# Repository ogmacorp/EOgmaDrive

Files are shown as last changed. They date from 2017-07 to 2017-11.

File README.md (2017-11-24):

<!---
  EOgmaDrive
  Copyright(c) 2017 Ogma Intelligent Systems Corp. All rights reserved.

  This copy of EOgmaDrive is licensed to you under the terms described
  in the EOGMADRIVE_LICENSE.md file included in this distribution.
--->

# EOgmaDrive

Repository for the EOgmaNeo-based self driving car (SDC).

Three sub-directories contain Readme.md files that further describes each configuration. A summary for each configuration is presented below.

Included are two configurations (1 & 2) used to build a 1/10 scale 2WD RC self driving car, and a third configuration to create a hand-sized 3D printed self driving car (uSDC).

**Configuration1** was used in producing the following Ogma YouTube video:

<a href="http://www.youtube.com/watch?feature=player_embedded&v=0ibVhtuQkZA
" target="_blank">Self Driving Car Learns Online and On-board on Raspberry Pi 3</a>

**Configuration3** appears in the first issue of the [HackSpace magazine](https://hackspace.raspberrypi.org/issues/1) (December 2017), as a project on [HackADay.io](https://hackaday.io/project/27173-a-self-driving-car-using-a-raspberry-pi-zero), and was used in producing the following Ogma YouTube video:

<a href="http://www.youtube.com/watch?feature=player_embedded&v=9GNbVkMb8Qw
" target="_blank">World's Smallest Self-Driving Car - a Raspberry Pi Zero on wheels..</a>

As seen in the above video, an [InfiniTrax](http://infinitrax.com/product.php) "1080 BEAST" modular track was used with the uSDC.

A [Unity](https://unity3d.com/) based simulation [OgmaDrive](https://github.com/ogmacorp/OgmaDrive) was used to prototype the SDC, using C# scripts and the EOgmaNeo library.

## Configuration1

- Steam Controller with wireless dongle

SDC:

- Traxxas Rustler RC car
- Raspberry Pi3
- Pi Camera v2
- Pi Camera case
- Active cooling case "Eleduino Raspberry Pi 3 and Raspberry Pi 2 Model B Acrylic Case with High Quality Mini Fan"
- 2 pcs 18650 batteries with battery pack (for powering the steering servo)
- Arduino UNO
- Breadboard
- Anker PowerCore 10000 (for powering the Pi)
- Using fast event-based version of EOgmaNeo + OpenCV's Canny Edge + PySerial (for Arduino communication)

RF Version Extra:

- Pi-Top with Raspberry Pi 3
- Arduino UNO (or Leonardo, USB to RPi)
- RF Transmitter/Receiver Modules "Makerfocus 2pcs Wireless Module NRF24L01+PA+LNA in Antistatic Foam Arduino Compatible with Antenna"

## Configuration2

Base station, for limited communication with the SDC:

- Pi-Top
- Raspberry Pi3
- Arduino UNO (or Leonardo, USB to RPi)
- XBee Arduino shield (v1.0 or modified v1.3)
- XBee Pro (S1, with u.fl antenna)

SDC:

- Traxxas Rustler RC car (optional clear body)
- Raspberry Pi3
- Raspberry Camera (mounted to front bumper)
- Pimoroni Pibow case
- Freetronics PiLeven (i2c to RPi, UART to XBee)
- XBee Arduino shield (v1.0 or modified v1.3)
- XBee Pro (S1, u.fl antenna)
- Power Bank (to PiLeven or RPi)
- Servo pass-through connector (attached to PiLeven)

## Configuration3

- Steam Controller with wireless dongle
- InfiniTrax modular track system (optional)

uSDC:

- 3D Printed base, RPi ZeroW mount, and camera mount
- Raspberry Pi ZeroW
- Pimoroni Explorer pHAT (motor drivers)
- Pololu 136:1 sub-micro planetary gearmotors, wheels, and front ball caster
- Adafruit Lithium Ion Polymer Battery, with a PowerBoost and charger module
- SainSmart wide angle camera

## License and Copyright

<br />The work in this repository is licensed under the <a rel="license" href="http://creativecommons.org/licenses/by-nc-sa/4.0/">Creative Commons Attribution-NonCommercial-ShareAlike 4.0 International License</a>. See the  [EOGMADRIVE_LICENSE.md](https://github.com/ogmacorp/EOgmaDrive/blob/master/EOGMADRIVE_LICENSE.md) and [LICENSE.md](https://github.com/ogmacorp/EOgmaDrive/blob/master/LICENSE.md) files for further information.

Contact Ogma via licenses@ogmacorp.com to discuss commercial use and licensing options.

EOgmaDrive Copyright (c) 2017 [Ogma Intelligent Systems Corp](https://ogmacorp.com). All rights reserved.

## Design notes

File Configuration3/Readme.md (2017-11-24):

<!---
  EOgmaDrive
  Copyright(c) 2017 Ogma Intelligent Systems Corp. All rights reserved.

  This copy of EOgmaDrive is licensed to you under the terms described
  in the EOGMADRIVE_LICENSE.md file included in this distribution.
--->

# Configuration3 (uSDC)



As seen in the first issue of the [HackSpace magazine](https://hackspace.raspberrypi.org/issues/1) (December 2017), and as a project on [HackADay.io](https://hackaday.io/project/27173-a-self-driving-car-using-a-raspberry-pi-zero)

## Bill of Materials

The [BillOfMaterials.md](BillOfMaterials.md) file details all the items required before assembly.

## Hardware Assembly

Refer to the [AssemblyInstructions.md](AssemblyInstructions.md) file for a detailed description of the assembly steps.

## Software Installation

The [SoftwareInstallation.md](SoftwareInstallation.md) file contains all the steps required to install and test package dependencies.

## Control of the uSDC

There are two Python3 scripts included in this repository to test the uSDC:

- motorTest.py - A script to test the Explorer pHAT, Steam controller, and drive the uSDC around.
- main.py - The main script containing using the EOgmaNeo library. Allowing for learning, inference, and self-driving on the RPi ZeroW.

### Steam controller daemon

Both of the included python scripts require the Steam controller daemon to be running. After the daemon has been started, it emulates the Steam controller as a Xbox controller. PyGame can then connect to and obtain joystick and button information. The motorTest.py and main.py scripts can then make use of the controller to drive the uSDC around.

Starting the daemon requires the following bash command:

```bash
sudo python3 ~/steamcontroller/scripts/sc-xbox.py start
```

and the following command to stop the daemon:

```bash
sudo python3 ~/steamcontroller/scripts/sc-xbox.py stop
```

### motorTest python script

To test the Steam controller and Explorer pHAT motor driver, the following commands and script can be used:

```bash
cd ~/EOgmaDrive/Configuration3
sudo python3 ~/steamcontroller/scripts/sc-xbox.py start
sudo python3 motorTest.py
sudo python3 ~/steamcontroller/scripts/sc-xbox.py stop
```

Similar controls as used in the main.py script are used here:

- The joystick controls left or right steering,
- Trigger buttons apply forward/backward drive,
- The `A` button cleanly exits the script.

The `trimming` global variable allows for trimming of the forward/backward motion, so that applying motion using the triggers ensures that the uSDC travels in a straight line.

## The main python script

The `main.py` Python3 script is used for training (manual driving) and inference (self driving). All processing occurs on the Raspberry Pi ZeroW board.

It can be started using the following bash commands:

```bash
cd ~/EOgmaDrive/Configuration3
sudo python3 ~/steamcontroller/scripts/sc-xbox.py start
sudo python3 main.py
sudo python3 ~/steamcontroller/scripts/sc-xbox.py stop
```

The uSDC can then be controlled using the Steam controller with:

- The analogue joystick controls left or right steering.
- Trigger buttons apply forward/backward drive.
- The `A` button toggles between training and prediction modes.
- The `B` button saves the current camera image.
- The `X` button saves the current state of the hierarchy.
- The `Y` button exits the script.

If you train and save out the current state of the hierarchy, that saved state can be reloaded by starting the script with a `load` parameter. For example:

```bash
sudo python3 main.py load
```

**Note:** Saving the hierarchy to the a file on the SD card can take a minute or so to perform. Console text will announce when saving starts, and also when saving has completed.

If the uSDC doesn't travel in a straight line using one of the trigger buttons, a `trimming` global variable can be modified to compensate for any drift. For example this could be set to `trimming = 0.2`

An `RGB` image is captured from the camera module at each time step. This is converted into a grey scale image. And an EOgmaNeo pre-encoder (`ImageEncoder`) is used to transform the dense camera image into a sparse chunked representation, that alongside the current motor values, is sent into the EOgmaNeo predictive hierarchy.

When the `A` button is initially pressed the `training` global variable is toggled. And instead of using the Steam controller input to steer the uSDC and send values into the EOgmaNeo predictive hierarchy (training mode), the hierarchy's prediction of the next motor steering values are used (inference mode). Be aware that during inference mode a constant forward drive is applied to both motors. Pressing the `A` button again can toggle back to training mode.

## Testing the uSDC

Online learning only occurs within the `main.py` script and the EOgmaNeo predictive hierarchy when forward drive is active. To navigate around a track, a number of laps are required before the predictive hierarchy can confidently make steering predictions.

With learning only enabled during forward motion, it's possible to reverse out of steering mistakes made when driving around a track.

The more laps of a track that occur during training mode, the more confident the predictive hierarchy will be when switching to inference mode (that is, steering only use hierarchy output predictions and current camera input).

As seen in our YouTube video of the uSDC, we use an [InfiniTrax](http://infinitrax.com/product.php) modular track to perform more elaborate training and inference testing.

<a href="http://www.youtube.com/watch?feature=player_embedded&v=9GNbVkMb8Qw
" target="_blank">World's Smallest Self-Driving Car - a Raspberry Pi Zero on wheels..</a>

The simplest way to check that everything is working is to perform the following:

1. Apply constant left/right steering.
1. Apply forward drive so that the uSDC spins on the spot.
1. After 30-60 seconds, release the joystick and trigger button.
1. Press the `A` button, and the uSDC should spin on the spot.
1. Press the `A` button again to toggle back to training mode.

Try the above but steering in the opposite direction. And test out saving and reloading of the hierarchy to see whether it remembers how to spin on the spot.

## License and Copyright

<br />The work in this repository is licensed under the <a rel="license" href="http://creativecommons.org/licenses/by-nc-sa/4.0/">Creative Commons Attribution-NonCommercial-ShareAlike 4.0 International License</a>. See the  [EOGMADRIVE_LICENSE.md](https://github.com/ogmacorp/EOgmaDrive/blob/master/EOGMADRIVE_LICENSE.md) and [LICENSE.md](https://github.com/ogmacorp/EOgmaDrive/blob/master/LICENSE.md) file for further information.

Contact Ogma via licenses@ogmacorp.com to discuss commercial use and licensing options.

EOgmaDrive Copyright (c) 2017 [Ogma Intelligent Systems Corp](https://ogmacorp.com). All rights reserved.

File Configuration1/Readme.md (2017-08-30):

<!---
  EOgmaDrive
  Copyright(c) 2017 Ogma Intelligent Systems Corp. All rights reserved.

  This copy of EOgmaDrive is licensed to you under the terms described
  in the EOGMADRIVE_LICENSE.md file included in this distribution.
--->

# Configuration1

Parts:

- Traxxas Rustler 
- Raspberry Pi 3
- Anker Powercore 10000
- Arduino Uno R3
- Steam Controller (w/ dongle)
- Elduino Pi 3 case with mini fan
- Pi Camera v2
- Pi Camera Case (blue)
- 2x EBL 18650 3.7v 3000mAh Li-ion Rechargable Batteries (for Arduino)
- 18650 2 battery holder
- Miscellaneous: Wires, breadboard, charger (for 18650), double-sided foam tape, crimps

## Overview of Configuration

The Steam controller is used to remotely control the car for training. The Pi communicates with the Arduino using serial, where the Pi sends the Arduino motor commands for the steering/throttle. The Anker PowerCore powers the Pi 3, and high-drain 18650 Li-ion batteries are used to power the Arduino/servo/ESC (not enough amps from just the PowerCore).

An older version of this configuration had the Steam controller communicate with a Pi-Top instead of the car directly, and then used a radio module to communicate with the car. However, just using the steam controller directly improved responsiveness and range is sufficient. The Steam controller dongle is now plugged directly into the Pi 3, where it uses an Xbox360 emulation driver to allow Pygame to detect it [https://github.com/ynsta/steamcontroller](https://github.com/ynsta/steamcontroller).

- SDC\_Transmitter.ino contains the old transmitter code for the older RF version of this configuration (no longer used)
- SDC\_controller.ino contains the old receiver code for the older RF version of this configuration (no longer used)
- SDC\_controller\_norf.ino contains the final (no RF) code used in the Arduino
- SDC3\_sc.py, sdc\_fast\_line.py, and sdc\_master\_sc.py contain the Pi 3 controller scripts. These are all variations of each other, but the sdc\_fast\_line version performs the best.

Images:

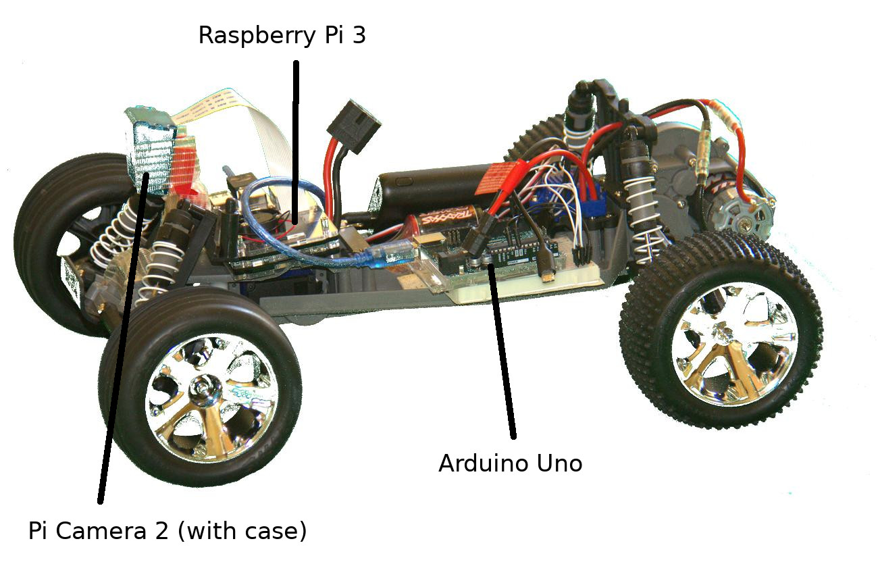
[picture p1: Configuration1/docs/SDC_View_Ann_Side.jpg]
View1


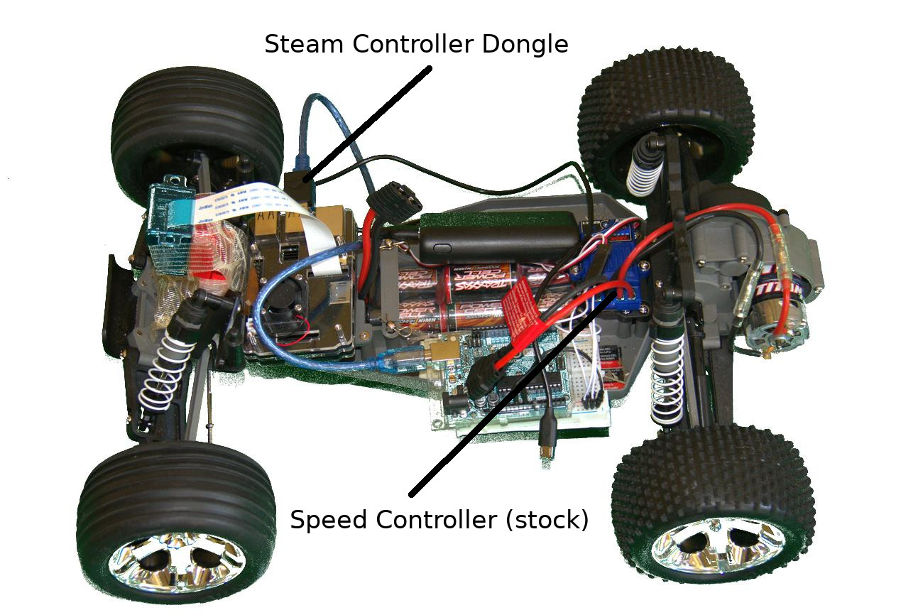
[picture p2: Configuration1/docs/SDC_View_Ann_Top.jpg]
View2


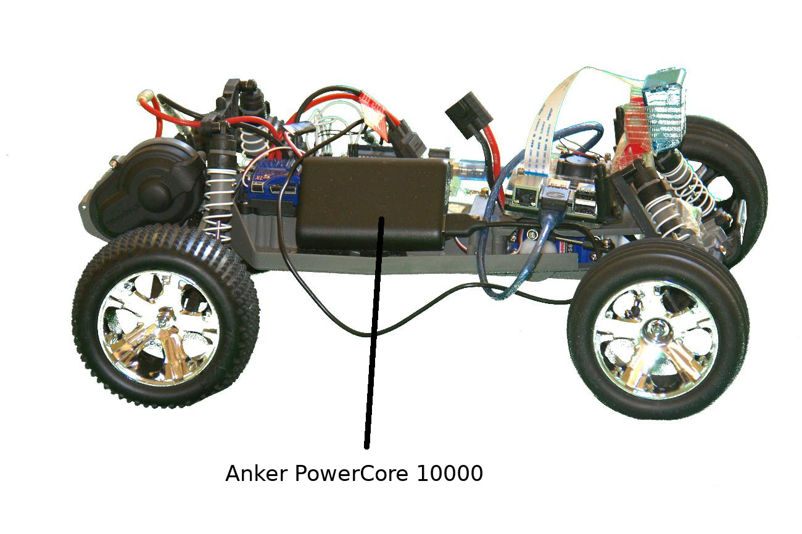
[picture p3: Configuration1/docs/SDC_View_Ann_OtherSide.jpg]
View3


## License and Copyright

<br />The work in this repository is licensed under the <a rel="license" href="http://creativecommons.org/licenses/by-nc-sa/4.0/">Creative Commons Attribution-NonCommercial-ShareAlike 4.0 International License</a>. See the  [EOGMADRIVE_LICENSE.md](https://github.com/ogmacorp/EOgmaDrive/blob/master/EOGMADRIVE_LICENSE.md) and [LICENSE.md](https://github.com/ogmacorp/EOgmaDrive/blob/master/LICENSE.md) file for further information.

Contact Ogma via licenses@ogmacorp.com to discuss commercial use and licensing options.

EOgmaDrive Copyright (c) 2017 [Ogma Intelligent Systems Corp](https://ogmacorp.com). All rights reserved.

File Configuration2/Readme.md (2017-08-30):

<!---
  EOgmaDrive
  Copyright(c) 2017 Ogma Intelligent Systems Corp. All rights reserved.

  This copy of EOgmaDrive is licensed to you under the terms described
  in the EOGMADRIVE_LICENSE.md file included in this distribution.
--->

# Configuration2

# Base station

The PiTop base station is only required to toggle between training and prediction modes on the SDC. And to optionally allow for a SSH shell, and/or remote desktop, into the SDC RPi for diagnostic purposes.

- [Pi-Top](https://pi-top.com)
- [Raspberry Pi3](https://www.raspberrypi.org)
- [Arduino](https://www.arduino.cc) UNO (or Leonardo, connected via USB to RPi)
- [XBee Arduino shield](https://www.arduino.cc/en/Main/ArduinoXbeeShield) (v1.0 or modified v1.3)
- [XBee Pro](https://www.digi.com/lp/xbee) (Series 1, with u.fl antenna)
- [USB WIFI (802.11 b/g/n) adapter](https://thepihut.com/products/usb-wifi-adapter-for-the-raspberry-pi) (Optional)

Image 1: PiTop with an Arduino Uno and XBee Pro RF module and antenna.  
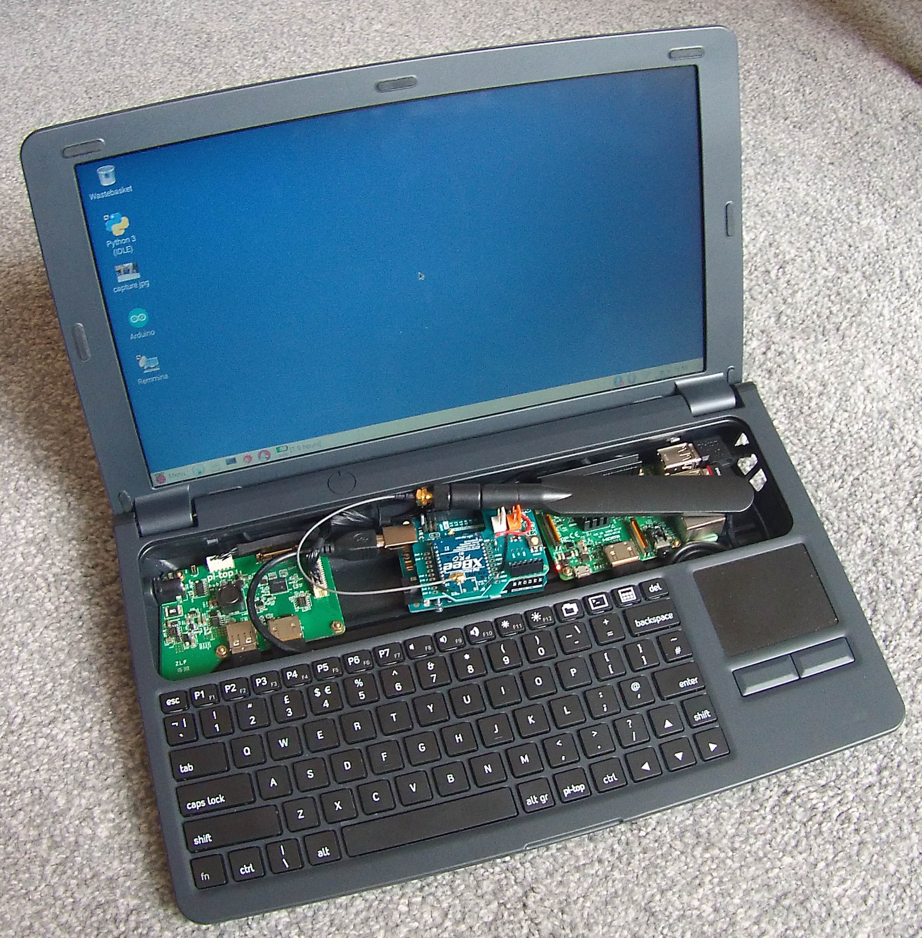
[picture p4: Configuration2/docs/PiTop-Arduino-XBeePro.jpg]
PiTop


## Optional: Pi-Top as a WiFi Access Point and DHCP server

The Raspibery Pi3 installed into the Pi-Top can be setup as a WiFi access point and DHCP server. This allows for the RPi on the SDC to wirelessly connect to the Pi-Top RPi, and for a SSH shell to be created on the Pi-Top RPi.

Instructions for how to set this up can be found here: https://learn.adafruit.com/setting-up-a-raspberry-pi-as-a-wifi-access-point/overview

Connection range is limited when using WiFi, so this is only required to be able to access the SDC RPi when on the field/track.

## Arduino XBee Shields

Using an Arduino board that uses a single UART for both USB and shield communication (D0 and D1), such as the Uno or Duemilanove, requires modification to the shield dependant on the version:

- v1.0 ./docs/XbeeShieldSchematic.pdf  
For the v1.0 version of the shield it is simply a case of removing the jumpers on JP2 and JP3. Then connecting pin 2 of JP2 to pin 3 of J1 (D2 on the Arduino), and pin 2 of JP3 to pin 4 of J1 (D3 on the Arduino).

- v1.3 ./docs/Arduino_Shield_Xbee_Rev1_3.pdf  
For the v1.3 version of the shield two tracks need to be cut (tracks B and E out of SW1). Then connecting pin 2 of XB1 to pin 3 of J1 (D2 on the Arduino), and pin 2 of IC2 to pin 4 of J1 (D3 on the Arduino).

This modification then allows the Arduino SoftwareSerial library to use D2 (Rx) and D3 (Tx) to communicate exclusively with the XBee Pro.

*NOTE 1:* When using the XBee shield with the PiLeven this modification is not required. The PiLeven and RPi can communicate via an i2c interface.  
*NOTE 2:* An alternative method would be to use an Arduino Leonardo. That creates a CDC-ACM USB connection with the RPi, leaving the Leonardo UART to be used with the XBee Pro.

## PiTop to SDC communication

PiTop RPi Python serial connection to the Arduino (over USB). Arduino connection to the XBee Pro RF module. Upload the `Configuration2/PiTop_XBee_CommTest` sketch to the Arduino. Use the Arduino IDE Serial Monitor to send the following key commands to the SDC Arduino:

- `T` to enter training mode,
- `P` to enter prediction mode,
- `S` to receive the Actual and Predicted steering and throttle values.
- `V` to receive information on the steering and throttle PWM signals.

# SDC

Image 2: The Traxxas Rustler showing the front bumper mounted Raspberry Pi3 camera, blue RF antenna that connects to the Traxxas stock controller, and the black top mounted XBee Pro antenna that connects to the PiTop-housed XBee Pro module.  
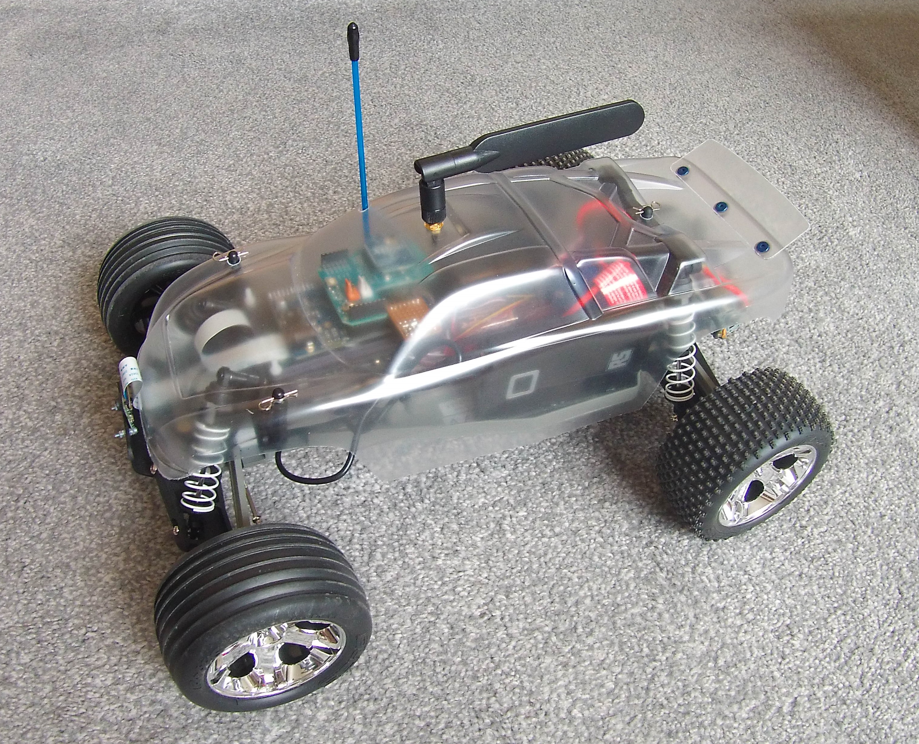
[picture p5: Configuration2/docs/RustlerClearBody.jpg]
Traxxas Rustler
 

- [Traxxas Rustler](https://traxxas.com/products/models/electric/37054rustler) RC car (optional clear body)
- [Raspberry Pi3](https://www.raspberrypi.org) (v2, FOV 62.2x48.8 degrees)
- [Raspberry Pi Camera](https://www.raspberrypi.org/products/camera-module-v2/) (mounted to front bumper)
- [Pimoroni Pibow case](https://shop.pimoroni.com/collections/pibow)
- [Freetronics PiLeven](https://www.freetronics.com.au/collections/raspberry-pi/products/pileven-arduino-compatible-expansion-for-raspberry-pi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) (Arduino compatble, i2c to RPi, UART to XBee)
- [XBee Arduino shield](https://www.arduino.cc/en/Main/ArduinoXbeeShield)
- [XBee Pro](https://www.digi.com/lp/xbee) (Series 1, with u.fl antenna)
- [Power Bank](http://uk.rs-online.com/web/p/power-banks/7757508/) (at least 2A @ 5V, to PiLeven or RPi)
- Servo pass-through connector (attached to PiLeven)

Image 3: Internal components - RPi3 in a grey Pimoroni Pibow case, connected to a PiLeven RPi hat, connected to a XBee Pro RF module and shield, a protoboard servo pass-through connecter intercepting the front servo and ESC connections, a front bumper mounted RPi camera v2, and a 2A Power bank for powering the RPi3 and PiLeven.  
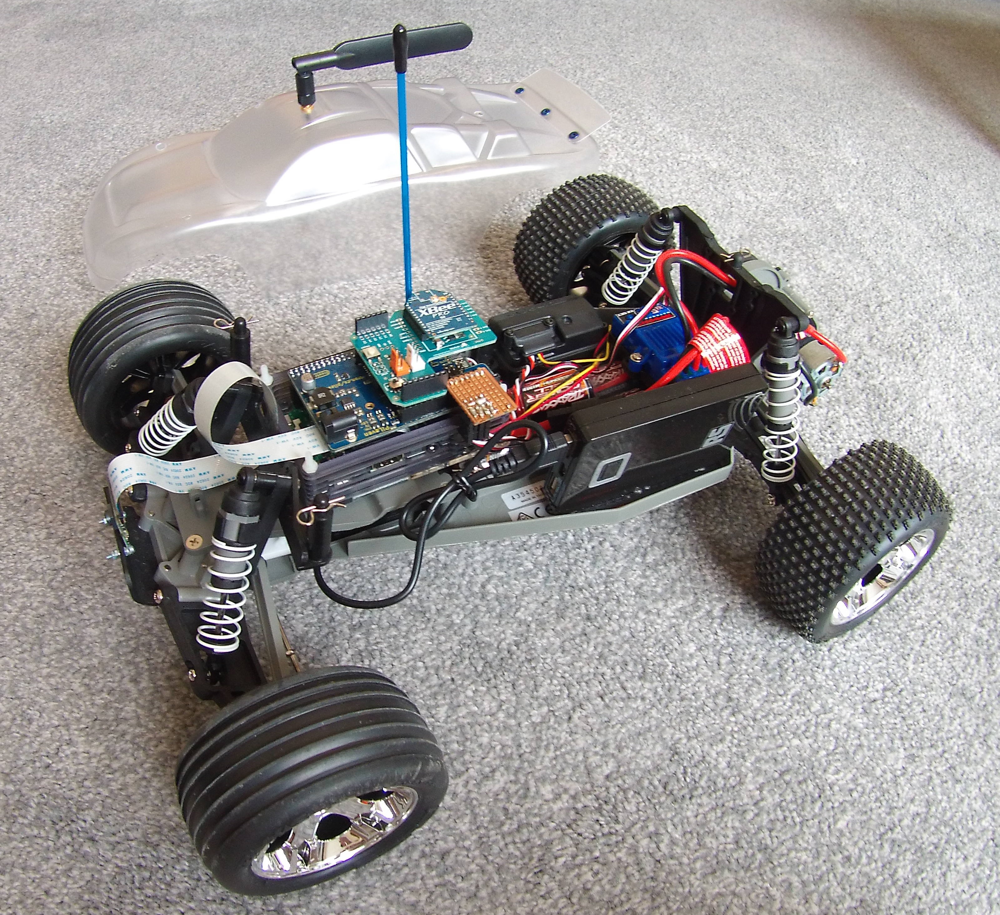
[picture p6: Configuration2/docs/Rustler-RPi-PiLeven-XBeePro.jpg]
Internal setup


## PiLeven (Arduino) RPi hat

Using a PiLeven RPi hat allows for the use of i2c communications with the SDC RPi. Freeing up the PiLeven UART for use by the XBee Pro RF unit.

### PiLeven_XBee_CommTest

Python SMBus library for Wire (i2c) communication between RPi and PiLeven. PiLeven (Arduino) Serial UART to XBee Pro communication.

https://github.com/freetronics/PiLeven/wiki/I2C

## Servo pass-through connector

The front steering servo connection with the Traxxas Rustler RF module is intercepted via headers soldered to the PiLeven. With Gnd and Power pass-through, and the signal line connected via D8 and D9 shield connections with the PiLeven (Arduino).

This allows for the PiLeven to monitor the steering PWM signal coming from the Traxxas RF module. This monitored PWM signal is sent to the SDC RPi for input into the EOgmaNeo library, and the predicted steering angle out of EOgmaNeo can then be passed back from the RPi to the PiLeven, to be used as the alternative steering PWM signal. During training the monitored PWM signal can be passed directly though to the front steering servo.

## Throttle pass-through connector

The ESC XL5 motor controller connection with the Traxxas Rustler RF module is intercepted via headers soldered to the PiLeven. With Gnd and Power pass-through, and the signal line connected via D10 and D11 shield connections with the PiLeven (Arduino).

## SDC RPi Controller script

The `RPi_Controller.py` Python script is the main software controlling:
- the EOgmaNeo learning algorithm, 
- communication with the PiLeven and XBee Pro RF module,
- handling the RPi camera image stream (Yuv format, only Y/Luminance used),
- using Pillow to perform edge-filtering of the Luminance camera image,
- receiving steering angles from the PiLeven,
- predicting steering angles and forwarding to the PiLeven.

The `PiLeven_Controller` Arduino sketch requires uploading to the PiLeven via the Arduino IDE. It handles:
- communication with the SDC RPi and XBee Pro RF module,
- sends steering value to the SDC RPi,
- receives predicted steering value from the SDC RPi,
- receives via the XBee Pro commands from the Pi-Top.

# Misc

## Python packages

Install OpenCV via https://github.com/jabelone/OpenCV-for-Pi
> pip3 install -r requirements.txt

## Traxxas Rustler vs Unity Stockcar dimensions

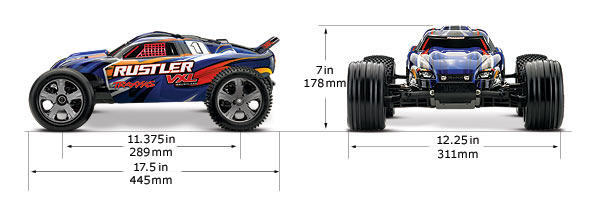
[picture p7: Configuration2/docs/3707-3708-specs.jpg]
Rustler dimensions
  
http://rustlervxlguide.blogspot.co.uk/2012/03/rustler-vxl-specs-from-traxxas.html

| | Traxxas Rustler | Unity Stockcar model |
|---|---|---|
| Length | 44.5 cm | 2 units |
| Width  | 31.1 cm | 0.75 units |
| Height | 17.8 cm | 0.6 units |

## License and Copyright

<br />The work in this repository is licensed under the <a rel="license" href="http://creativecommons.org/licenses/by-nc-sa/4.0/">Creative Commons Attribution-NonCommercial-ShareAlike 4.0 International License</a>. See the  [EOGMADRIVE_LICENSE.md](https://github.com/ogmacorp/EOgmaDrive/blob/master/EOGMADRIVE_LICENSE.md) and [LICENSE.md](https://github.com/ogmacorp/EOgmaDrive/blob/master/LICENSE.md) file for further information.

Contact Ogma via licenses@ogmacorp.com to discuss commercial use and licensing options.

EOgmaDrive Copyright (c) 2017 [Ogma Intelligent Systems Corp](https://ogmacorp.com). All rights reserved.

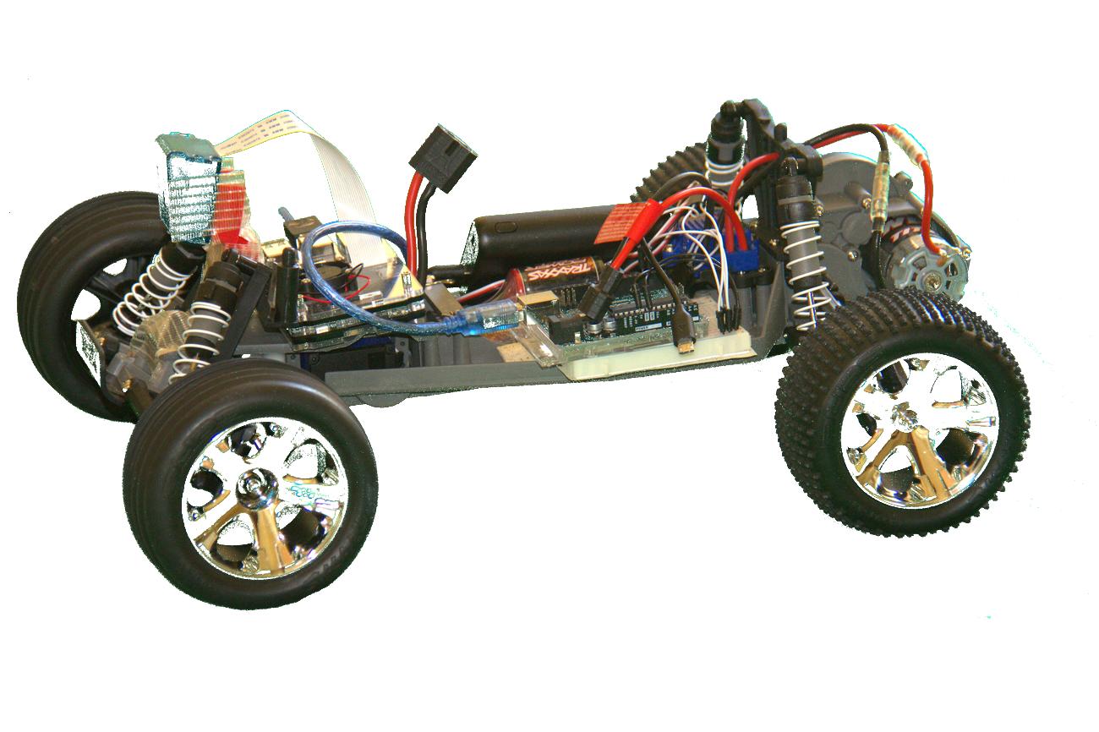
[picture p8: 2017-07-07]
Configuration1/docs/SDC_View_Side.jpg

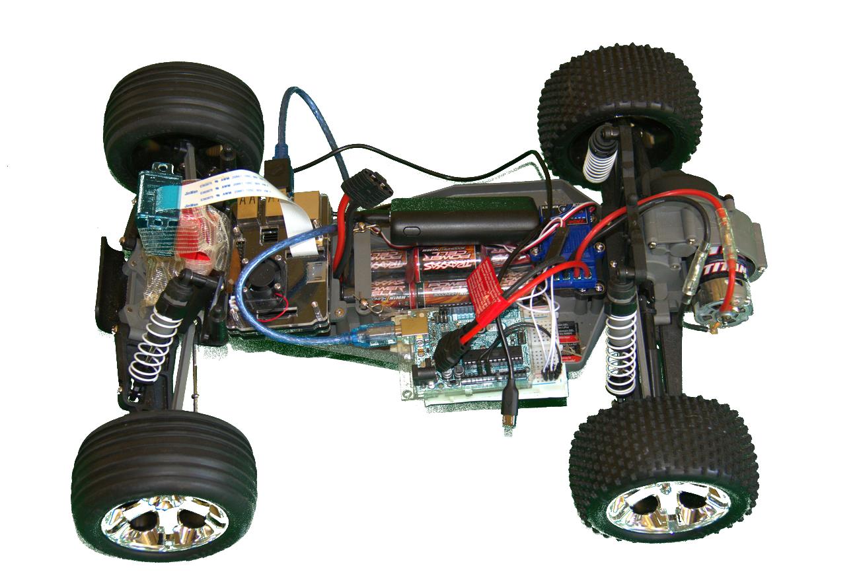
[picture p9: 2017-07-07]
Configuration1/docs/SDC_View_Top.jpg

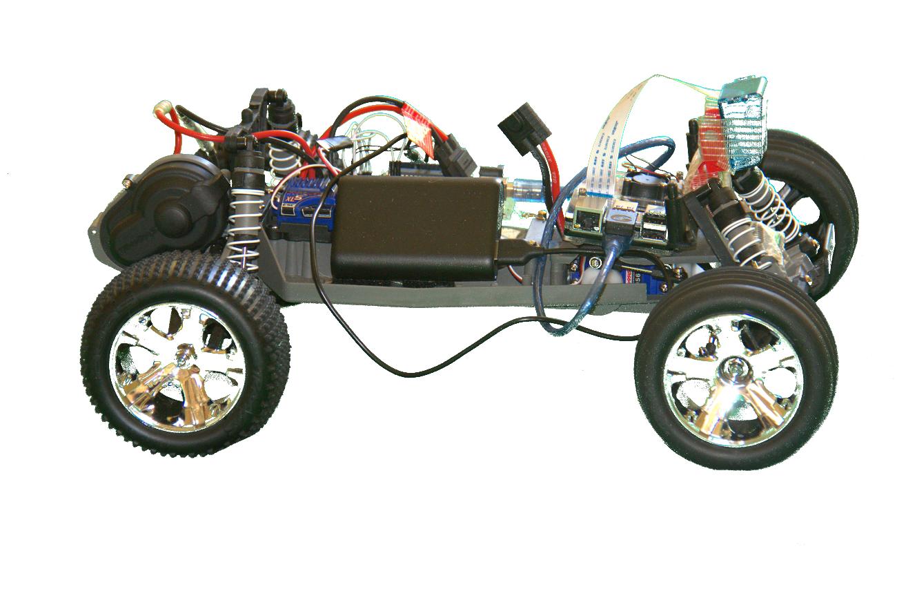
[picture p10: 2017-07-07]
Configuration1/docs/SDC_View_OtherSide.jpg

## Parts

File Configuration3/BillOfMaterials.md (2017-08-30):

<!---
  EOgmaDrive
  Copyright(c) 2017 Ogma Intelligent Systems Corp. All rights reserved.

  This copy of EOgmaDrive is licensed to you under the terms described
  in the EOGMADRIVE_LICENSE.md file included in this distribution.
--->

# Configuration3 (uSDC)



## Bill of Materials

Refer to the following tables for details of the numbered items in this image:
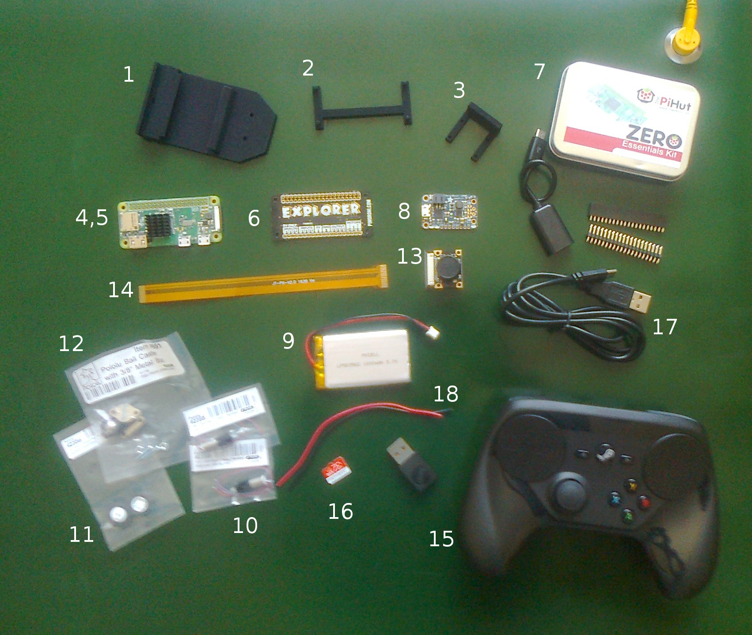
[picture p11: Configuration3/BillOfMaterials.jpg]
Bill Of Materials


### 3D printed parts

| Item # | STL Filename | Description |
| --- | --- | --- |
| 1 | base.stl | Main base for the uSDC |
| 2 | piMount.stl | Mounting frame for Pi ZeroW |
| 3 | camMount.stl | Mount for RPi camera |

Notes:

1. The main base part has three through holes: One rear diagonal hole that allows the motor cables to thread through from the mounting cylinder for the motors. And two front holes (13.462mm spacing) for mounting the ball caster.
1. The Pi ZeroW and Camera mounting parts require the appropriate glue to position them onto the base platform. The type/kind of glue is dependant on the material used when 3D printing all the parts. For example, when a Nylon PA2200 based material is used Araldite (epoxy adhesive) is recommended.

### Electro-mechanical parts

| Item # | Manufacturer | Description | Part # |
| --- | --- | --- | ---: |
| 4 | [Raspberry Pi](https://www.raspberrypi.org/) | Main processing board | [Zero W](https://www.raspberrypi.org/products/raspberry-pi-zero-w/) |
| 5 | - | Heatsink for the Raspberry Pi Zero Broadcom CPU (~6mm height) | [example](https://shop.pimoroni.com/products/heatsink) |
| 6 | [Pimoroni](https://shop.pimoroni.com/) | Pi Zero HAT containing two H-bridge motor drivers | [Explorer pHAT](https://shop.pimoroni.com/products/explorer-phat) |
| 7 | [The Pi Hut](https://thepihut.com/) | Pi Zero Essentials Kit that *importantly* includes a male MicroUSB to female USB adapter, and dual-row male and female GPIO headers | [Zero Essentials Kit](https://thepihut.com/products/raspberry-pi-zero-essential-kit) |
| 8 | [Adafruit](https://www.adafruit.com/) | PowerBoost 1000 Charger - Rechargeable 5V Lipo USB Boost @ 1A - 1000C | [2465](https://www.adafruit.com/product/2465) |
| 9 | [Adafruit](https://www.adafruit.com/) | Lithium Ion Polymer Battery - 3.7v 1200mAh | [258](https://www.adafruit.com/product/258) |
| 10 | [Pololu](https://www.pololu.com/) | (x2) 136:1 Sub-Micro Plastic Planetary Gearmotor 6Dx19L mm | [2358](https://www.pololu.com/product/2358) |
| 11 | [Pololu](https://www.pololu.com/) | 14×4.5mm Wheel Pair for Sub-Micro Plastic Planetary Gearmotors | [2356](https://www.pololu.com/product/2356) |
| 12 | [Pololu](https://www.pololu.com/) | Ball Caster with 3/8″ Metal Ball | [951](https://www.pololu.com/product/951) |
| 13 | [Sain Smart](https://www.sainsmart.com/) | Wide Angle FOV160° 5MP Camera Module | [101-40-113](https://www.sainsmart.com/sainsmart-wide-angle-fish-eye-camera-lenses-for-raspberry-pi-arduino.html) |
| 14 | [Sain Smart](https://www.sainsmart.com/) | Camera Cable for Raspberry Pi Zero | [101-40-199](https://www.sainsmart.com/raspberry-pi/camera-module/sainsmart-expansion-development-board-support-arduino-xbee-for-raspberry-pi-a-pi-b-pi-2-model-b-pi-3-model-b.htm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) |
| 15 | [Valve](http://www.valvesoftware.com/) | Steam Controller (includes a USB dongle) | [info](http://store.steampowered.com/app/353370/Steam_Controller/) |
| 16 | - | Raspberry Pi Zero compatible micro SD / SDHC card | [examples](http://www.raspberry-pi.co.uk/2012/06/07/compatible-sd-cards/) |
| 17 | - | USB to microUSB data cable (connecting a PC/Laptop to the Pi Zero) | |
| 18 | - | Power hook-up wires (connecting the PowerBoost to Explorer pHAT) | |
| - | - | Tools, e.g. solder and iron, wire cutter, glue, non-conductive Velcro/foam tape, etc. | |
| - | - | Nuts and bolts (for connecting the camera module to the mounting part), e.g. M2 x 10/12mm

Notes:

1. Although the motor shafts have a flattened key on them, the motor wheels do not. Therefore it's typical to use a small amount of glue to attach the wheels to the motor shaft. Be careful not to push/bleed glue into the motor gearbox casing.

### Modular track system (optional)

We used an [InfiniTrax](http://infinitrax.com/product.php) (http://infinitrax.com/product.php) "1080 BEAST" modular track system for testing the uSDC. This track can be seen in the YouTube video of the uSDC - https://www.youtube.com/watch?v=9GNbVkMb8Qw

## License and Copyright

<br />The work in this repository is licensed under the <a rel="license" href="http://creativecommons.org/licenses/by-nc-sa/4.0/">Creative Commons Attribution-NonCommercial-ShareAlike 4.0 International License</a>. See the  [EOGMADRIVE_LICENSE.md](https://github.com/ogmacorp/EOgmaDrive/blob/master/EOGMADRIVE_LICENSE.md) and [LICENSE.md](https://github.com/ogmacorp/EOgmaDrive/blob/master/LICENSE.md) file for further information.

Contact Ogma via licenses@ogmacorp.com to discuss commercial use and licensing options.

EOgmaDrive Copyright (c) 2017 [Ogma Intelligent Systems Corp](https://ogmacorp.com). All rights reserved.

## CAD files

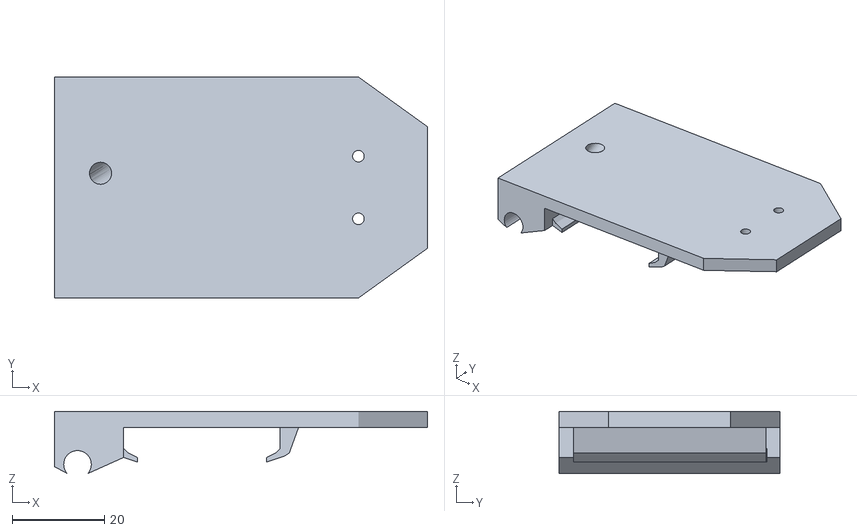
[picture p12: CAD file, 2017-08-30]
Configuration3/base.stl
81.0 x 48.0 x 13.5

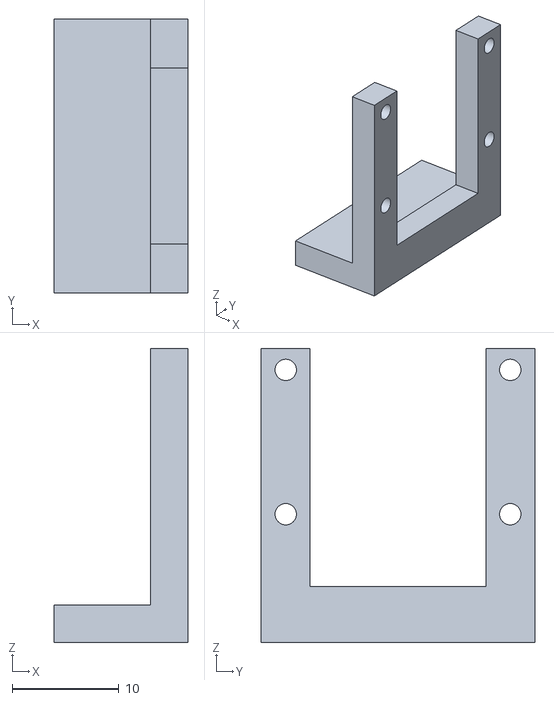
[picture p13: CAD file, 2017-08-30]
Configuration3/camMount.stl
12.5 x 25.6 x 27.5

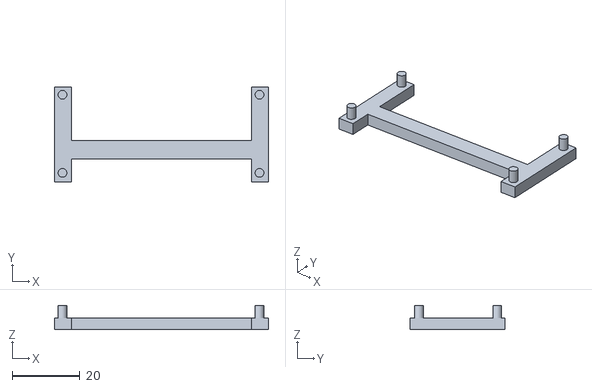
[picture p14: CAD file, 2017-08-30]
Configuration3/piMount.stl
63.0 x 28.0 x 7.21

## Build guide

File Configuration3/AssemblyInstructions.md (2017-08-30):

<!---
  EOgmaDrive
  Copyright(c) 2017 Ogma Intelligent Systems Corp. All rights reserved.

  This copy of EOgmaDrive is licensed to you under the terms described
  in the EOGMADRIVE_LICENSE.md file included in this distribution.
--->

# Configuration3 (uSDC)



## Bill of Materials

Refer to the [BillOfMaterials.md](BillOfMaterials.md) for all the items required before assembly.

## Hardware assembly

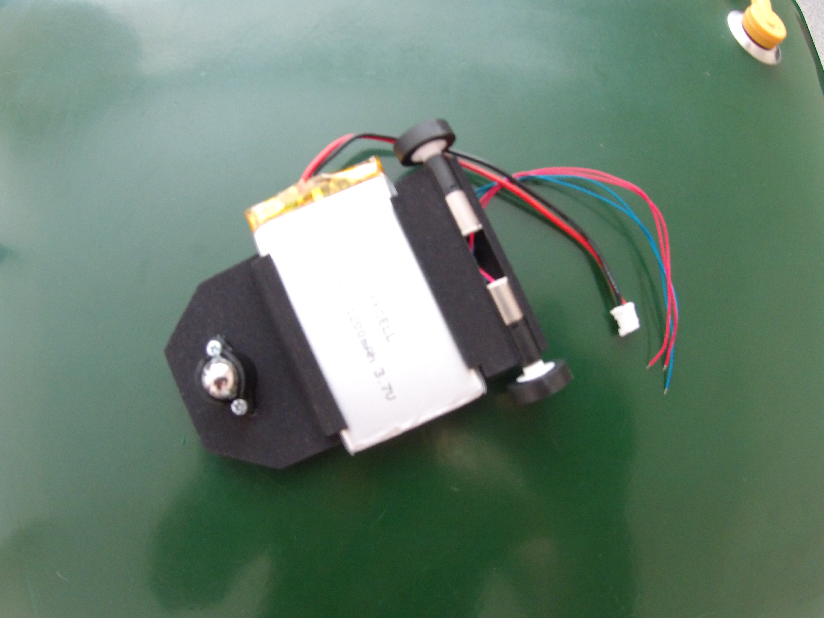
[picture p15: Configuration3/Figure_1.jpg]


Figure 1,

- Glue the wheels to the Pololu motors. Take care not to get any glue into the black motor gearbox casing.
- Slot the motors into the base. Feed the motor cables through the hole in the base.
- Bolt the Pololu ball caster to the base. Use the larger spacing plate supplied with the ball caster.
- Slide the Adafruit LiPo battery into the base.

<br>

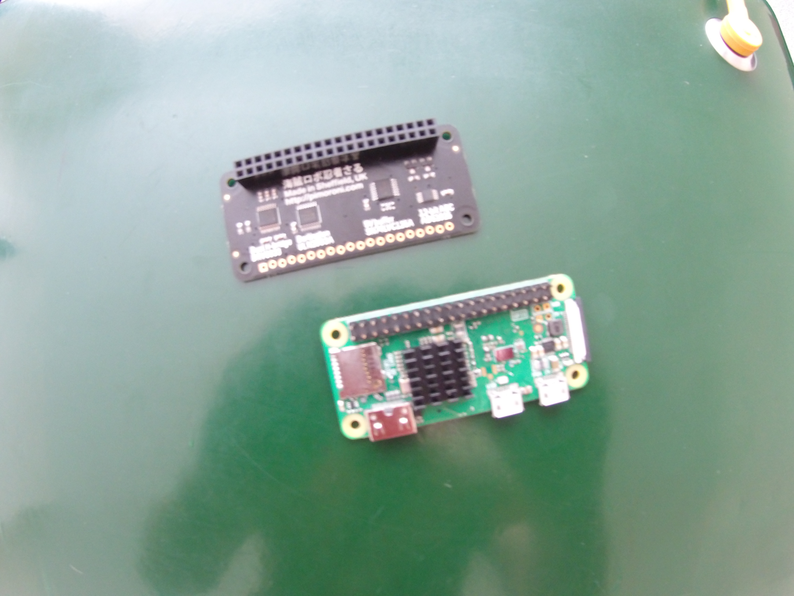
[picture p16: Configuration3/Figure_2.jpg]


Figure 2,

- Solder GPIO headers onto the Raspberry Pi ZeroW (male header) and Explorer pHAT (female header).
- Stick a heat sink onto the Pi ZeroW Broadcom CPU.

<br>

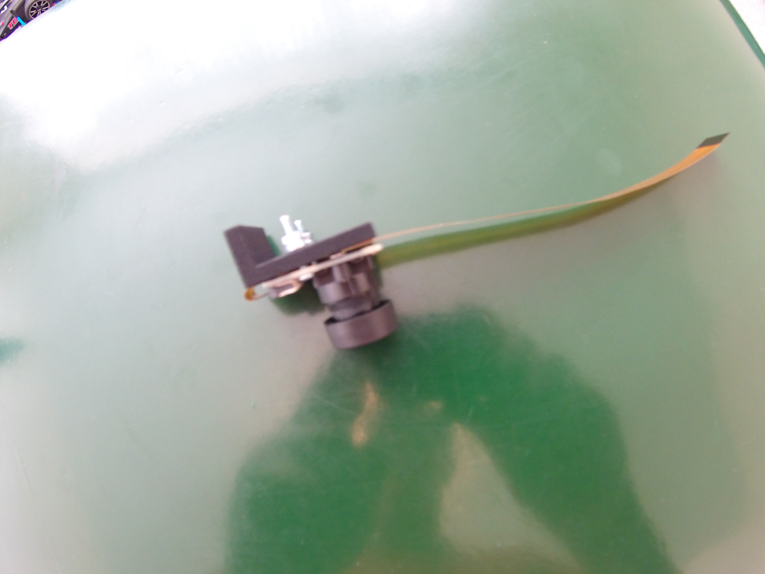
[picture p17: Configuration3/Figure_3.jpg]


Figure 3,

- Attach the camera cable to the camera module.
- Bolt the SainSmart camera board to the 3D printed mounting part.
- Connect the camera cable to the Raspberry Pi ZeroW.

<br>

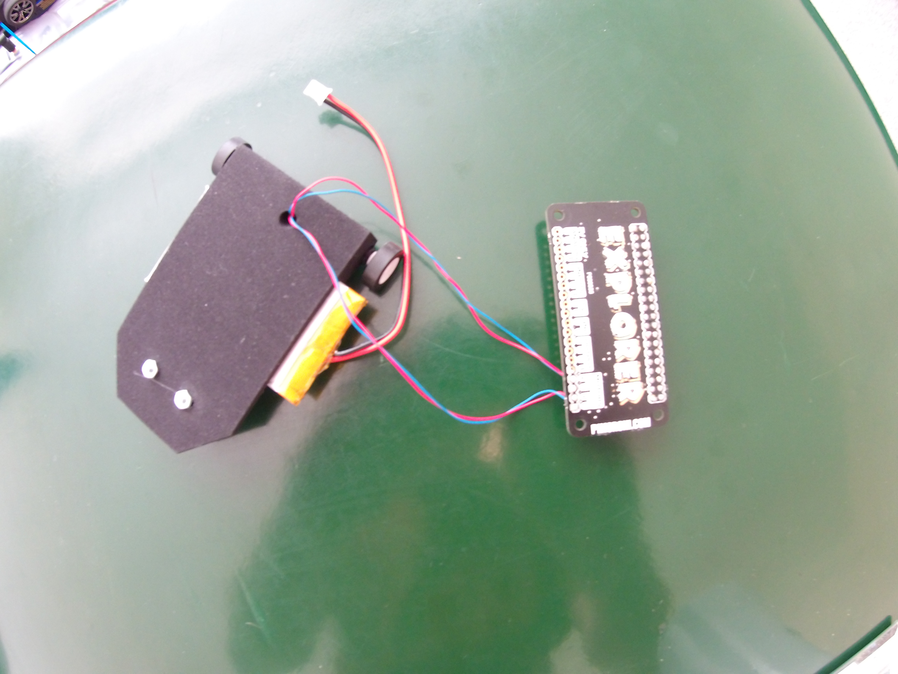
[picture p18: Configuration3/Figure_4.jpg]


Figure 4,

- Solder the motors cables to the Explorer pHAT.
  - <span style="color:cyan">Blue</span> wires to the Explorer pHAT `Motor-` and <span style="color:red">Red</span> wires to the Explorer pHAT `Motor+`

<br>

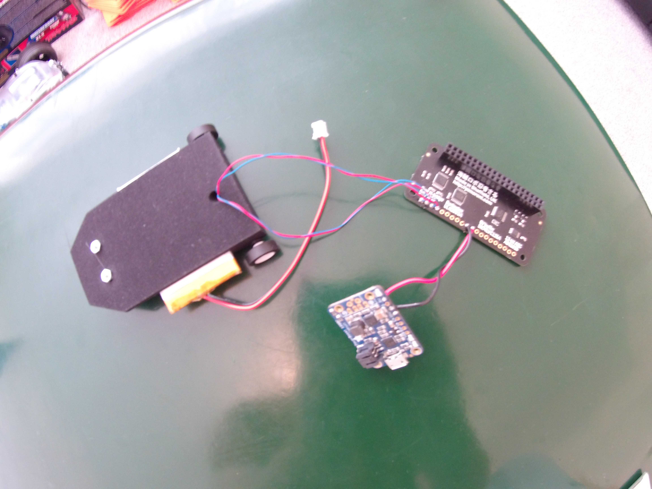
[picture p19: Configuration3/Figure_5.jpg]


Figure 5,

- Solder the Adafruit Powerboost connections to the Explorer pHAT.
  - Gnd to Gnd (black wire),
  - 5V and 5V (red wire).
- This step completes all the soldering work, so make sure that all connections are complete.

<br>

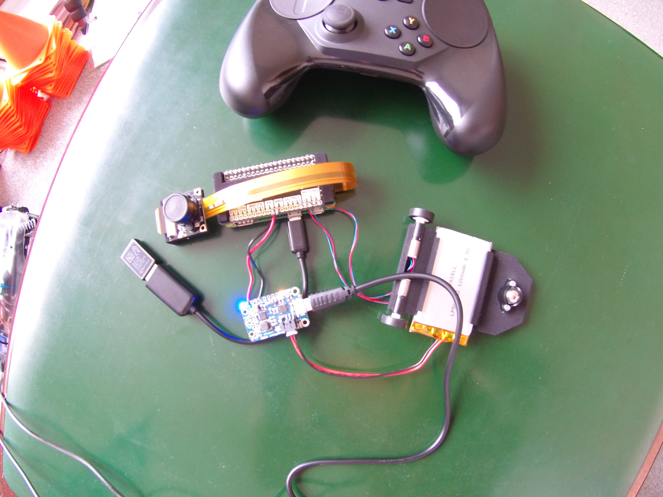
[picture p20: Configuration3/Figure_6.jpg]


Figure 6, Final connection checks and battery charging.

- Connect the Steam Controller dongle to the Raspberry Pi ZeroW `usb` connector.
- Attach the Explorer pHAT to the Raspberry Pi ZeroW
- Connect the LiPo battery to the Powerboost JST connector.
  - The Powerboost <span style="color:cyan">Blue</span> LED should light up.
  - The <span style="color:lime">Green</span> LED on the Raspberry Pi ZeroW will light and flash as it boots into the Raspbian Jessie (Lite) OS.
- Connect a PC/Laptop to the Powerboot USB.
  - The Powerboost <span style="color:orange">Orange</span> LED will light to show that it is charging the LiPo battery.
  - The Powerboost <span style="color:orange">Orange</span> LED will change to <span style="color:lime">Green</span> when charging is complete.

Notes:

- The Powerboost USB connection can be removed once the battery has been charged. The Powerboost will then continue to supply battery power to the Raspberry Pi ZeroW.
- Enabling WiFi on the Raspberry Pi ZeroW will allow for SSH shell access into it. See the [SoftwareInstallation.md](SoftwareInstallation.md) file for further details.

<br>

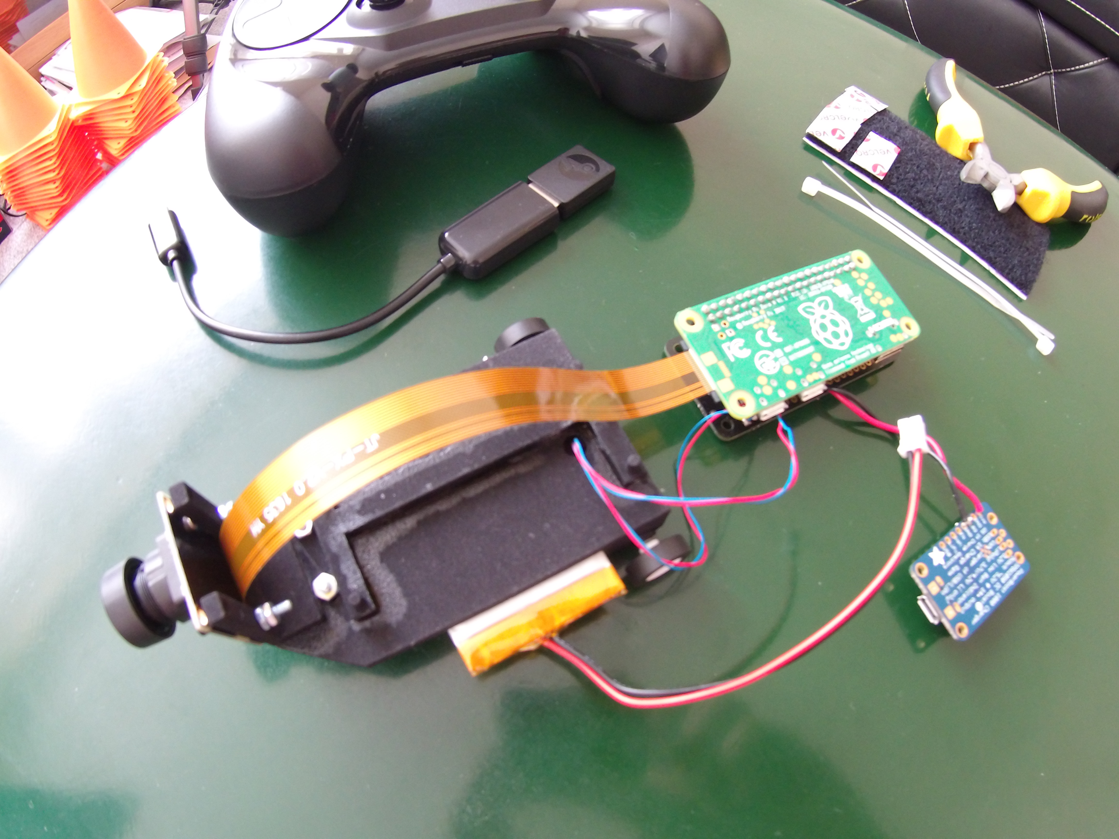
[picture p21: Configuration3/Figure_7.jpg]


Figure 7,

- Glue the Camera mount to the front of the base.
- Glue the Pi mount onto the base part.

<br>

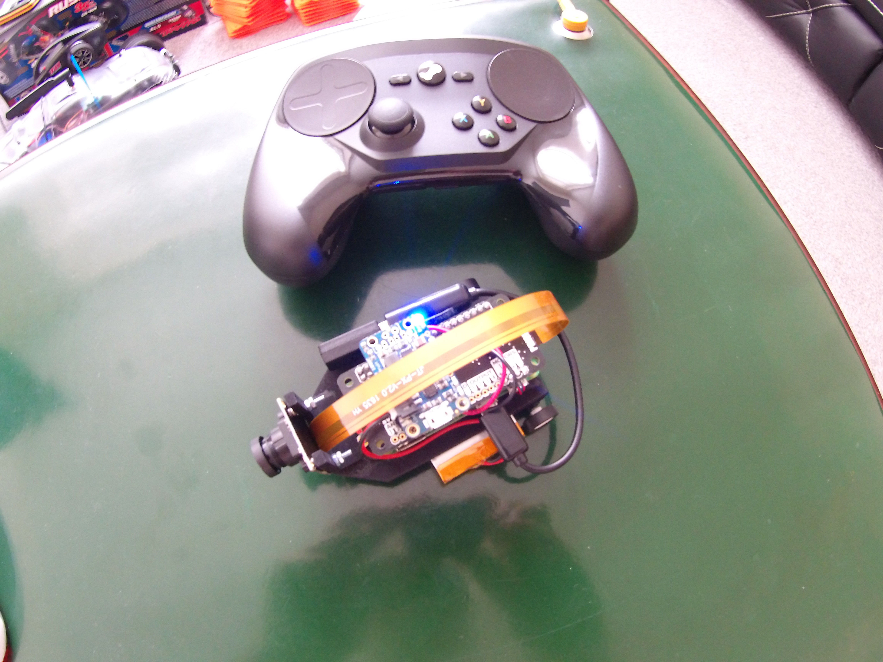
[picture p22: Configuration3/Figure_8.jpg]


Figure 8,

- Place the Raspberry Pi ZeroW and Explorer pHAT, onto the mounting part.
- Mount/Velcro the Powerboost board on top of the Explorer pHAT.
- Re-connect the Steam Controller dongle to the Raspberry Pi ZeroW. Zip-tie/Velcro it in place.
- Re-connect the LiPo battery to the Powerboost JST connector.

<br>

**Congratulations!** The build is complete.

The next steps are described in the [SoftwareInstallation.md](SoftwareInstallation.md) file.

## License and Copyright

<br />The work in this repository is licensed under the <a rel="license" href="http://creativecommons.org/licenses/by-nc-sa/4.0/">Creative Commons Attribution-NonCommercial-ShareAlike 4.0 International License</a>. See the  [EOGMADRIVE_LICENSE.md](https://github.com/ogmacorp/EOgmaDrive/blob/master/EOGMADRIVE_LICENSE.md) and [LICENSE.md](https://github.com/ogmacorp/EOgmaDrive/blob/master/LICENSE.md) file for further information.

Contact Ogma via licenses@ogmacorp.com to discuss commercial use and licensing options.

EOgmaDrive Copyright (c) 2017 [Ogma Intelligent Systems Corp](https://ogmacorp.com). All rights reserved.

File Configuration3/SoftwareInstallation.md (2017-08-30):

<!---
  EOgmaDrive
  Copyright(c) 2017 Ogma Intelligent Systems Corp. All rights reserved.

  This copy of EOgmaDrive is licensed to you under the terms described
  in the EOGMADRIVE_LICENSE.md file included in this distribution.
--->

# Configuration3 (uSDC)



## Software setup

Once the assembly instructions ([AssemblyInstructions.md](AssemblyInstructions.md)) have been finished the Raspberry Pi ZeroW can be setup with the appropriate software.

### Jessie image setup

Prepare the Raspberry Pi ZeroW for access via the command line:

- Download [Raspbian Jessie image](https://www.raspberrypi.org/downloads/raspbian/).
- Flash the image to a micro SD card.
- Edit the config.txt and configure.txt boot files, and create the empty `ssh` file. To allow for SSH over USB (e.g. https://gist.github.com/gbaman/975e2db164b3ca2b51ae11e45e8fd40a).
- Configure WiFi (e.g. https://raspberrypi.stackexchange.com/questions/62933/set-up-a-raspberry-pi-zero-w-without-monitor-or-ethernet-module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).

### Create a SSH shell into the Pi Zero

- Connect the Raspberry Pi ZeroW `usb` port (not the `pwr`) to a PC/laptop using a USB data cable.
- Use `ssh pi@raspberrypi.local` (or `ssh pi@raspberrypi` if configured to use WiFi). Alternatively use PuTTY, for example, to create a SSH shell into the device.

### Update Jessie

On the Pi ZeroW, use the following commands to configure and update it:

- Run `sudo raspi-config` to configure the Pi Zero. Options to change:
  - `5 Interfacing Options` -> `P1 Camera` to enable the Camera interface.
  - `7 Advanced Options` -> `A1 Expand Filesystem` to make sure it uses all of your SD card.
- Run `sudo apt update` followed by `sudo apt upgrade`, to make sure all packages are up to date.
- Use `sudo shutdown -h now` to power off the device.

### Install support packages

#### Common dependencies

```bash
sudo apt-get install cmake git python-dev python3-dev
```

#### Explorer pHAT

The easiest way is using the following command:
```
curl https://get.pimoroni.com/explorerhat | bash
```

Choose `y` (yes) for **all** questions asked by this bash script. The script will initial make sure that your Jessie image contains all the required packages (e.g. Python & Pip, Python3 & Pip3, and the I2C hardware interface is enabled).

Choosing `y` (yes) to the full install questions installs all the necessary Python(3) packages/dependencies required by the Explorer pHAT, its examples and documentation. Dependencies include packages such as PyGame, Git, SMBus, Cap1xxx, and ExplorerHat.

Upon completion of the bash script it should print "All Done. ...". At this point it is possible to check the motor connections using:

```python
$ python
>>> import explorerhat
Explorer pHAT detected...
>>> explorerhat.help()
...
>>> explorerhat.help("motor")
...
>>> explorerhat.motor.one.speed(10)
10
>>> explorerhat.motor.one.speed(0)
0
>>> explorerhat.motor.two.speed(10)
10
>>> explorerhat.motor.two.speed(0)
0
>>> exit()
```

Full installation instructions can be found here - https://github.com/pimoroni/explorer-hat

#### Camera Python module

Installation of the Python packages can be done using:

```bash
sudo apt-get install python-picamera python3-picamera
```

The following "Basic Recipe" (http://picamera.readthedocs.io/en/release-1.13/recipes1.html) can be used to capture an image using the SainSmart camera:

```python
$ cd ~
$ python
>>> from time import sleep
>>> from picamera import PiCamera
>>> camera = PiCamera()
>>> camera.resolution = (1024, 768)
>>> camera.start_preview()
>>> sleep(2)
>>> camera.capture('foo.jpg')
>>> exit()
```

From a host computer the following command can be used to obtain the image:
> scp pi@raspberrypi:/home/pi/foo.jpg ./foo.jpg

Further information about this Python interface can be found here: http://picamera.readthedocs.io/en/release-1.13/

#### Steam Controller

Stany Marcel's `Standalone Steam Controller Driver` is used to obtain control information from the controller using Python. It can be found on Github here: https://github.com/ynsta/steamcontroller

The following is a copy of the installation instructions:

```bash
cd ~
sudo pip3 install libusb1
sudo pip install libusb1
sudo pip install enum34
git clone https://github.com/ynsta/steamcontroller.git
cd steamcontroller
sudo python3 setup.py install
```

Create the following udev rules in a new file called `/etc/udev/rules.d/99-steam-controller.rules`

```text
# Steam controller keyboard/mouse mode
SUBSYSTEM=="usb", ATTRS{idVendor}=="28de", GROUP="games", MODE="0660"

# Steam controller gamepad mode
KERNEL=="uinput", MODE="0660", GROUP="games", OPTIONS+="static_node=uinput"
```

Reload udev with:

```bash
sudo udevadm control --reload
sudo reboot
```

After the reboot, restart a SSH shell and use the following to make sure that the Steam controller and USB dongle are working:

```bash
cd ~
sudo python3 ~/steamcontroller/scripts/sc-dump.py
```

#### OpenCV with Python bindings

Building OpenCV fresh from source code can take ~9 hours on the Raspberry Pi ZeroW. Therefore, the recommended way is to use a pre-built package.

Jaimyn Mayer supplies a package for OpenCV 3.1.0 on Github. Installation instructions can be found here: https://github.com/jabelone/OpenCV-for-Pi

#### SWIG

This needs to be installed to allow for the creation of Python bindings for EOgmaNeo. The following can be used to install this required package:

```bash
sudo apt-get install swig3.0
```

#### EOgmaNeo library

The following commands can be used to install the EOgmaNeo library:

```bash
cd ~
git clone https://github.com/ogmacorp/EOgmaNeo.git
cd EOgmaNeo/Python
sudo python3 setup.py install
```

#### EOgmaDrive

Clone the EOgmaDrive repository, or a fork of the repo:

```bash
cd ~
git clone https://github.com/ogmacorp/EOgmaDrive.git
cd EOgmaDrive/Configuration3
```

### Setup complete

All the required packages and dependencies have now been setup, and EOgmaDrive is ready to be tested. Head back to the main [Readme.md](Readme.md) file for further details.

## License and Copyright

<br />The work in this repository is licensed under the <a rel="license" href="http://creativecommons.org/licenses/by-nc-sa/4.0/">Creative Commons Attribution-NonCommercial-ShareAlike 4.0 International License</a>. See the  [EOGMADRIVE_LICENSE.md](https://github.com/ogmacorp/EOgmaDrive/blob/master/EOGMADRIVE_LICENSE.md) and [LICENSE.md](https://github.com/ogmacorp/EOgmaDrive/blob/master/LICENSE.md) file for further information.

Contact Ogma via licenses@ogmacorp.com to discuss commercial use and licensing options.

EOgmaDrive Copyright (c) 2017 [Ogma Intelligent Systems Corp](https://ogmacorp.com). All rights reserved.

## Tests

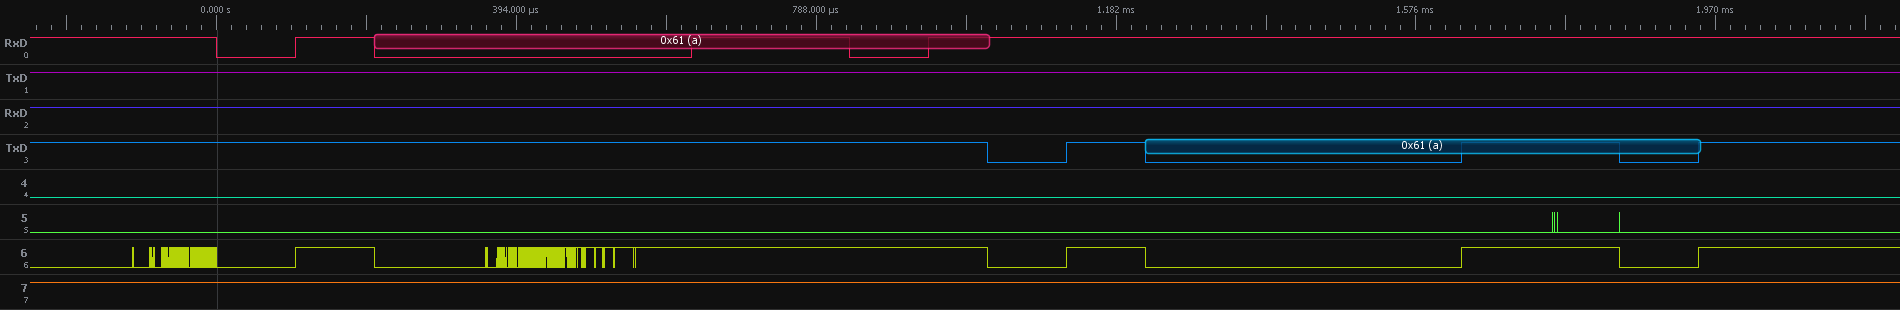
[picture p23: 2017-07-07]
Configuration2/PiTop_XBee_CommTest/OLS_capture.png

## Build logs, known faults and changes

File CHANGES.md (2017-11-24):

1.1.1 November, 2017
====================

- Links to HackSpace magazine article and HackADay project page

1.1  August, 2017
=================

- Addition of the uSDC configuration (RPi ZeroW version)

1.0.1 July, 2017
================

- Changes to match EOgmaNeo::System class renaming

1.0  July, 2017
====================

- Initial release

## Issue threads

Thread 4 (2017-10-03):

Avoiding obstcales

GoldenWings, 2017-10-03:
Does the current configuration supports identifying and avoiding obstacles? or the model needs some sort of ultrasound sensors and lidars?

222464, 2017-10-03:
We do not have explicit object detection. Rather, one has to train the model (preferrably in real-time/online) to avoid obstacles by just not driving into them and by correcting mistakes if the model drives close to them on its own (when in prediction mode).

Closed 2018-05-29.

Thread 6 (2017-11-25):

Toggling SDC mode after training causes car to move backwards (only)

aleonnet, 2017-11-25:
Hi,
Great project! I've implemented everything just like the instructions.
The motorTest.py works very well and I don't even need to use the trimming adjust.

However when I run main.py (EOgmaNeo predictive hierarchy) to try the spin on the spot test as instructed and press the A button to toggle to SDC mode, it simply goes backwards all the way.

What could have possibly gone wrong?

Thank you.

Also the left and right variables on motorTest.py and main.py have different signs. If I use the as main.py the left/right is inverted.

motorTest.py:
left = min(1.0, max(-1.0, drive * 0.5 - drive * steer * 0.5))
right = min(1.0, max(-1.0, drive * 0.5 + drive * steer * 0.5))

main.py:
left = min(1.0, max(-1.0, drive * 0.5 + drive * steer * 0.5))
right = min(1.0, max(-1.0, drive * 0.5 - drive * steer * 0.5))

222464, 2017-11-25:
Hello!

Try flipping the signs for the left and right motors in the code. left and right are basically just the "tank-like" steering commands for the motors, derived from a the more natural "car-like" steering used by the controller.  It's possible that the motor signs are not set up correctly in the code right now. I'll take a look at it tomorrow!

For now, look for this code:

```
explorerhat.motor[0].speed(int(sendLeftMotor` * trimMulLeft * powerScalar * 100))
explorerhat.motor[1].speed(-int(sendRightMotor * trimMulRight * powerScalar * 100))
```
And try different signs in front of the int(...) part.

Let me know how it goes!

aleonnet, 2017-11-27:
It worked, thank you!
I've inverted the signs of the code above, along with the previous change on the signs of 'left/sendLeftMotor' and 'right/sendRightMotor' formulas.
As a remark, I found it really difficult to control and train the model.

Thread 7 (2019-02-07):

Configuration3 (uSDC)

Ola1234, 2019-02-07:
So, im trying to make this car but i have a question, can i use other cameras? Like cheaper ones. If yes, can you link me? (~10$)

222464, 2019-02-07:
Hi,

Yes, you can use any camera compatible with the Pi Zero. I am not sure if there are any much cheaper than $20 though. Ideally it should be a wide-angle camera, like a fisheye camera.

Ola1234, 2019-02-07:
@222464 ok, thanks for the response.

Can It be these? https://m.banggood.com/en/1080P-5MP-160-Fish-Eye-Surveillance-Camera-Module-For-Raspberry-Pi-With-IR-Night-Vision-p-1234118.html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

222464, 2019-02-07:
@Ola1234 Yes, that should work, it looks like the fisheye camera we used actually.

Ola1234, 2019-02-07:
- @222464 Oh, Sorry for another question, but did i have to buy a steam controller? Because i have an chinese controller, like this one Dupad Story [2018 Updated] H9 2.4GHz Colorful Blacklit Mini Wireless Keyboard with Touchpad Mouse Combo, USB Rechargeable for Raspberry Pi,Google Android TV Box,HTPC,IPTV,PC,PAD,PS4 and More https://www.amazon.com/dp/B071FT92F8/ref=cm_sw_r_cp_apa_i_YikxCbMSG7B0X

222464, 2019-02-08:
@Ola1234 One of the reviews says that it worked for them on a Pi 3, so it will probably work here as well. Just make sure you get the proper adapter for the dongle (USB -> Micro USB).

222464, 2019-02-08:
@Ola1234 Oh, one thing I forgot to add: It seems that the controller you linked doesn't have an analog stick. This will make it more difficult to control the robot if you can only go full left/right or straight.

Closed 2020-05-16.

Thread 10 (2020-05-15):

Fixed drive throttle?

cfox570, 2020-05-15:
The code only predicts the steering with a fixed throttle. How would I also predict the throttle to drive the car?

222464, 2020-05-15:
Hi, you can predict it the same way as the steering if you like. I would recommend switching to [OgmaNeo2](https://github.com/ogmacorp/OgmaNeo2) though (the interface is very similar).

If you need help with the conversion to OgmaNeo2, let me know.

cfox570, 2020-05-15:
> Hi, you can predict it the same way as the steering if you like. I would recommend switching to [OgmaNeo2](https://github.com/ogmacorp/OgmaNeo2) though (the interface is very similar).
>
> If you need help with the conversion to OgmaNeo2, let me know.

I am not clear how to do that. The car driving code is in this repository. How would I change this code?

222464, 2020-05-15:
Which configuration are you trying to reproduce?

cfox570, 2020-05-15:
I am looking at the code in Configuration 1: sdc_fast_line.py

222464, 2020-05-15:
Ok, that code is quite old and still uses the old line segment detector pre-encoder. I wouldn't try to use it directly but rather as an example to base your own code on. For general usage on OgmaNeo2 (and in particular the Python bindings), check out [some of the examples.](https://github.com/ogmacorp/PyOgmaNeo2/blob/master/examples/WavyLinePrediction.py)

The steering (and throttle) can both be treated the same way as the line in the WavyLinePrediction demo - they are encoded into binned column representations and then fed to the hierarchy.

I will work on a proper tutorial - it seems it's about time to make one for the latest version of OgmaNeo2.

For now though, the general flow of OgmaNeo2 is as follows:

1. Fill out a list of LayerDesc(s)
2. Create a hierarchy with given input sizes and the list of LayerDesc(s)
3. (optional depending on task) create a pre-encoder to map certain sensory data to the CSDR format (e.g. an ImageEncoder)
4. encode sensory data into CSDRs via binning, pre-encoders, or other methods
5. call the hierarchy's step function with the sensory CSDRs
6. call getPredictionCs to get the predicted CSDRs (t + 1 prediction), use the prediction as needed
7. repeat 4 - 6.

I'll let you know when the tutorial is complete, it shouldn't take too long.

cfox570, 2020-05-15:
Thanks I will also take a look at the example

222464, 2020-05-16:
Just posted a basic tutorial, hopefully it helps: [tutorial](https://ogma.ai/2020/05/a-tutorial-on-ogmaneo2/)

Closed 2020-05-16.

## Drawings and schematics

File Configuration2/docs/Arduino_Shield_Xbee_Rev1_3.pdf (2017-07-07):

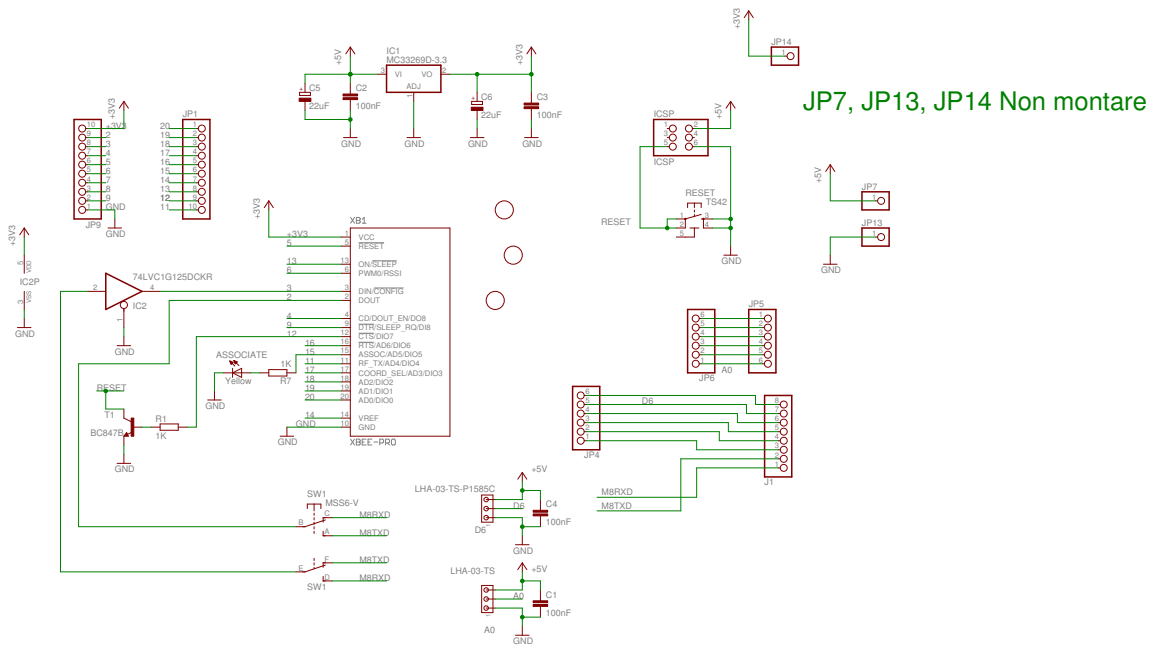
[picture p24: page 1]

+3V3 +5V +3V3 +5V GND GND GND GND GND GND +3V3 GND MC33269D-3.3 GND 1K BC847BGND 22uF 22uF +3V3 74LVC1G125DCKR GND +3V3 100nF 100nF MSS6-V 1K TS42 ICSP GND +5V Yellow LHA-03-TS-P1585C LHA-03-TS +5V +5V GND GND 100nF 100nF GND J112345678 VCC 1 DOUT 2 DIN/CONFIG 3 CD/DOUT_EN/DO8 4 RESET 5 PWM0/RSSI 6 DTR/SLEEP_RQ/DI8 9 GND 10 RF_TX/AD4/DIO4 11 CTS/DIO7 12 ON/SLEEP 13 VREF 14 ASSOC/AD5/DIO5 15 RTS/AD6/DIO6 16 COORD_SEL/AD3/DIO3 17 AD2/DIO2 18 AD1/DIO1 19 AD0/DIO0 20 JP4 123456 JP5123456 JP6 123456 JP71 JP112345678910 JP9 12345678910 IC1 ADJ VI 3 1 VO 2 R7 T1 C5 C6 JP131 JP141 2 4 1 IC2 5 3 IC2PVDD VSS C2 C3 C B A SW1F E D SW1 R1 12 34 5 RESET 1 2 3 4 5 6 ICSP ASSOCIATE 1 D6 1 A0 C1 C4 GND GND D6 D6 RESET RESET M8RXD M8RXD M8RXD M8TXD M8TXD M8TXD +3V3 +3V3 A0 A0 2 2 3 3 4 4 5 5 6 6 89 9 11 11 12 12 14 14 15 15 16 16 17 17 18 18 19 19 20 20 13 13 7 + + JP7, JP13, JP14 Non montare

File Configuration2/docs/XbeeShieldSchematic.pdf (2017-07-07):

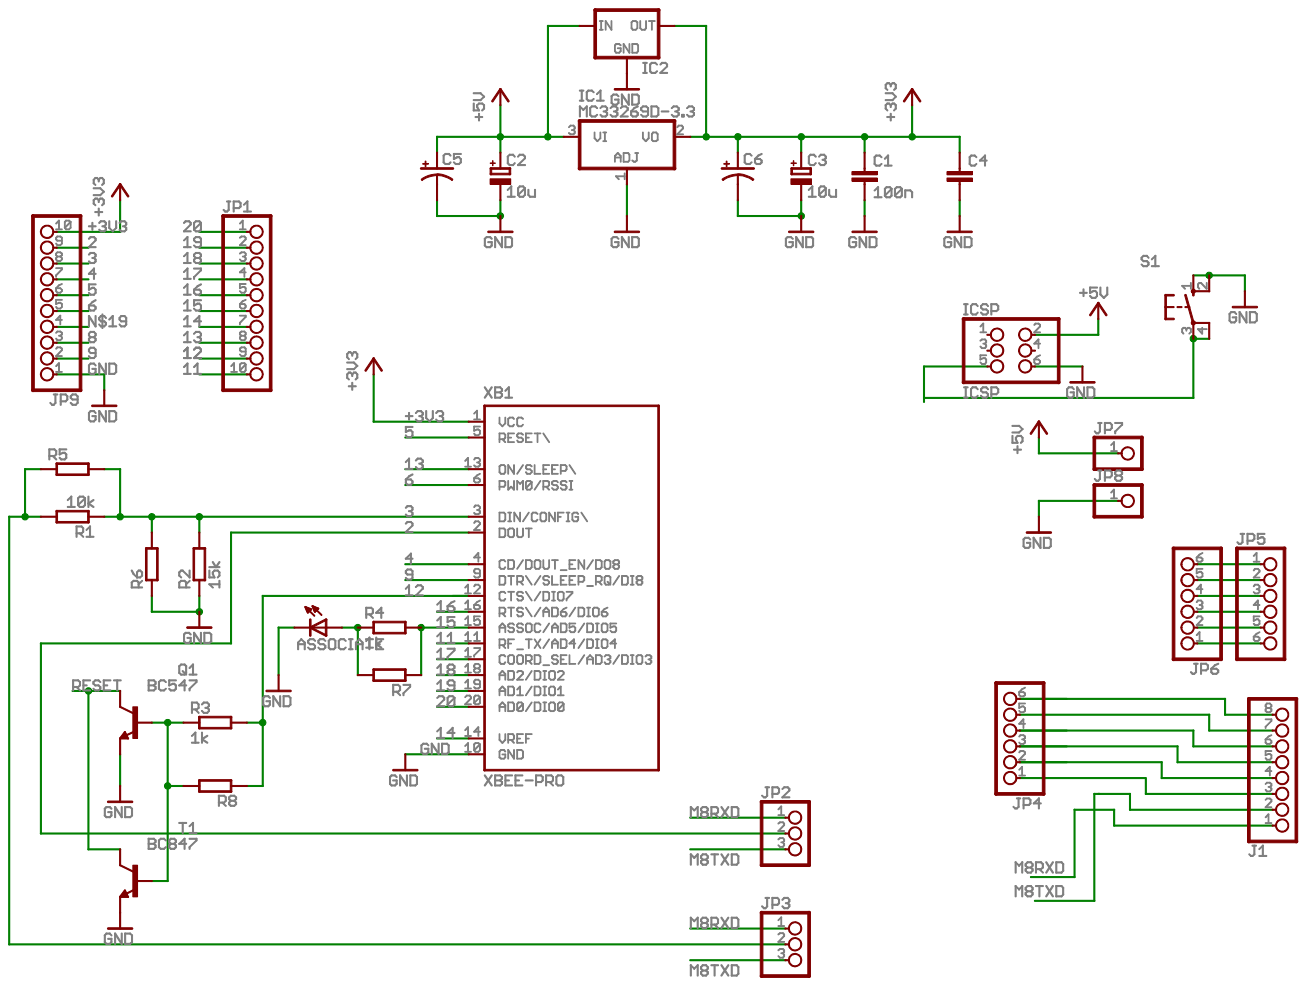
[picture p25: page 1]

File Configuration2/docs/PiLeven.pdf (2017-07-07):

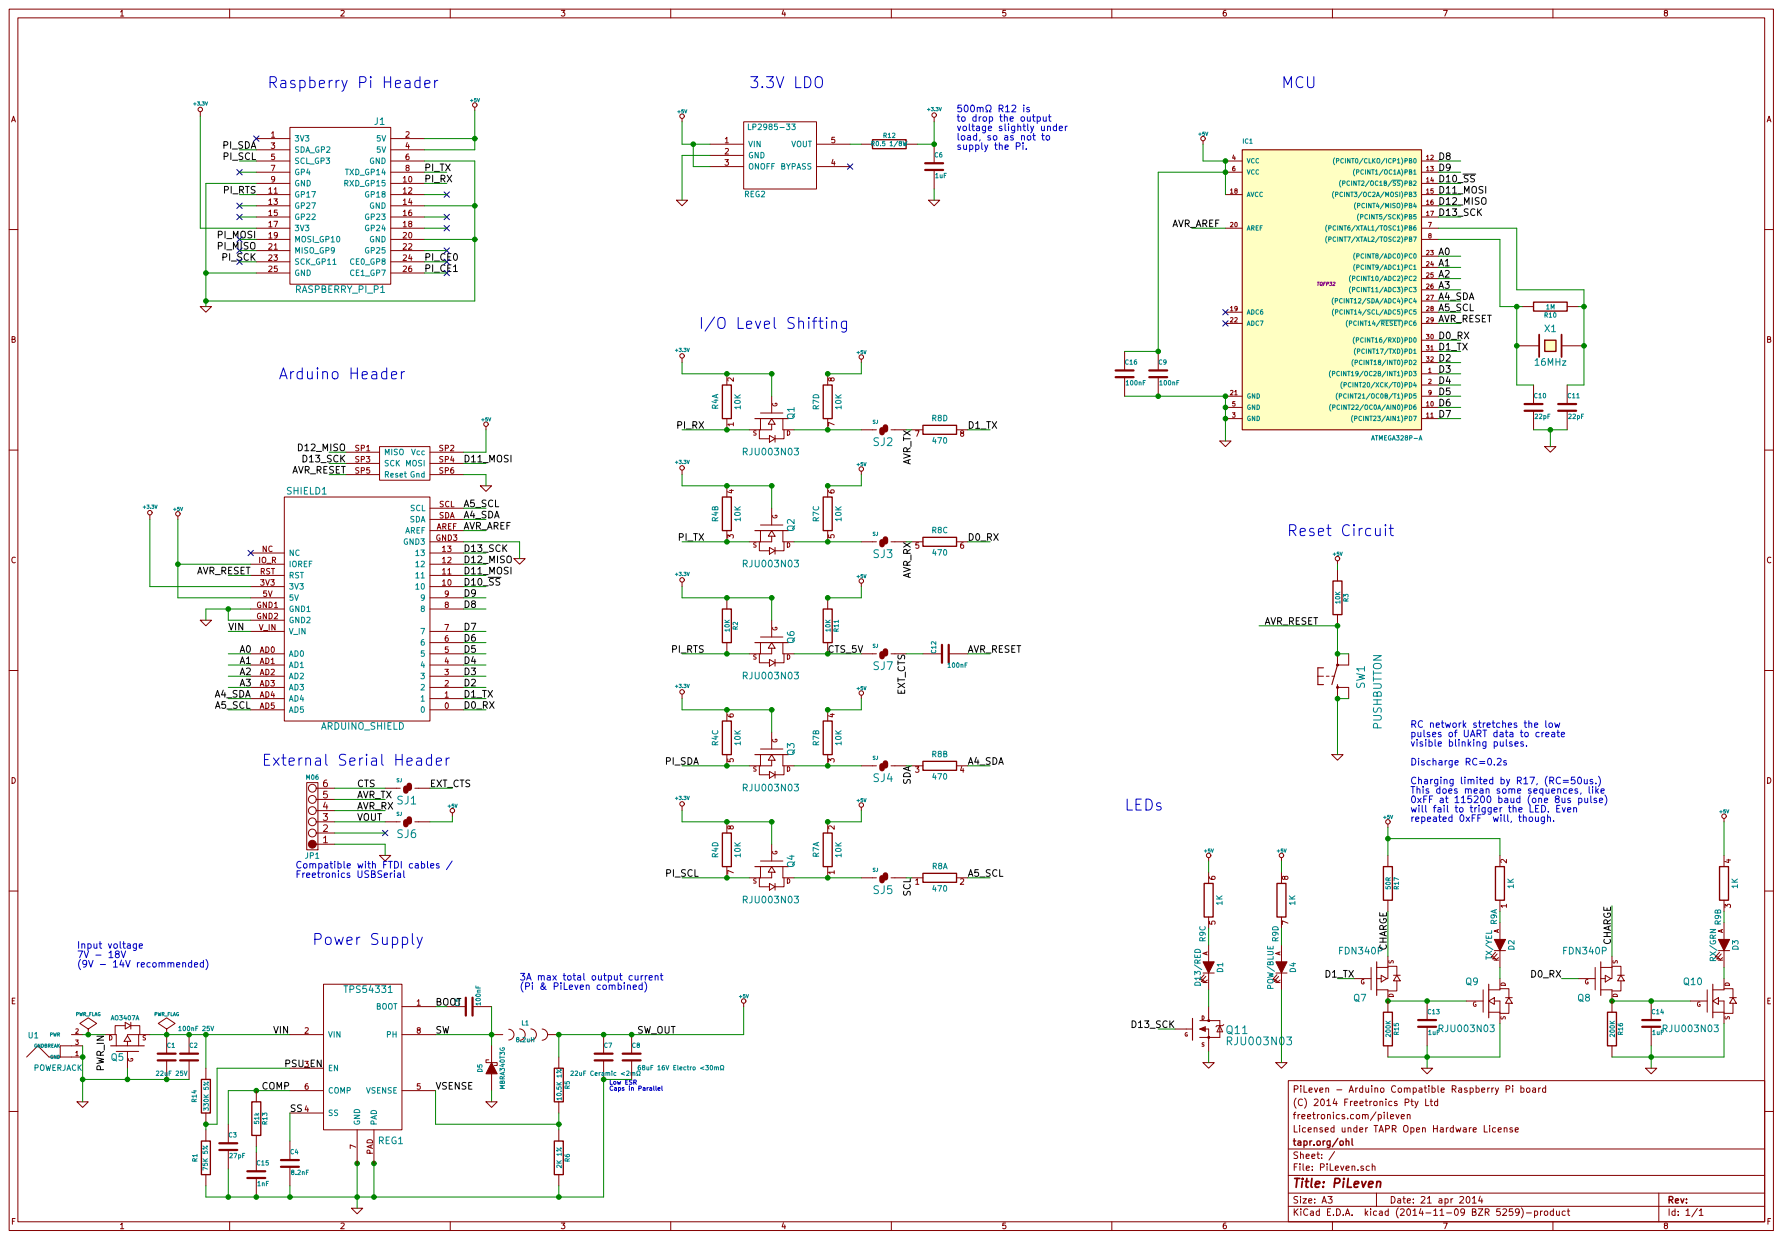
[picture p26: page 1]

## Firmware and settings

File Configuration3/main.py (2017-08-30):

# ----------------------------------------------------------------------------
#  EOgmaDrive
#  Copyright(c) 2017 Ogma Intelligent Systems Corp. All rights reserved.
#
#  This copy of EOgmaDrive is licensed to you under the terms described
#  in the EOGMADRIVE_LICENSE.md file included in this distribution.
# ----------------------------------------------------------------------------

# -*- coding: utf-8 -*-

import sys
import os
import signal
import pygame
import picamera
import pygame.surface
import pygame.joystick
import numpy as np
import struct
import re
import os.path
import eogmaneo
import time
import explorerhat
import cv2

loadExisting = len(sys.argv) > 1 and sys.argv[1] == "load"

if loadExisting:
    print("Called with load. Reloading a saved hierarchy, if it exists.")

######################
# Setup PyGame

os.environ["SDL_VIDEODRIVER"] = "dummy"
signal.signal(signal.SIGINT, signal.default_int_handler)

pygame.init()
os.putenv('SDL_VIDEODRIVER', 'fbcon')
pygame.display.init()

pygame.joystick.quit()
pygame.joystick.init()

joystick_count = pygame.joystick.get_count()

if joystick_count < 1:
    print("No joysticks found.")

    sys.exit()

print("Found " + str(joystick_count) + " joysticks.")

joy = pygame.joystick.Joystick(0)
joy.init()

######################
# Setup PiCamera

camera = picamera.PiCamera()

camWidth = 64
camHeight = 48

camera.resolution = (camWidth, camHeight)
camera.framerate = 24
#camera.rotation = 180

time.sleep(2)

######################
# Setup EOgmaNeo

esystem = eogmaneo.ComputeSystem(4)

ld = 2 * [ eogmaneo.LayerDesc() ]

for l in range(0, len(ld)):
    ld[l]._width = 24
    ld[l]._height = 24
    ld[l]._chunkSize = 6

    ld[l]._forwardRadius = 9
    ld[l]._backwardRadius = 9

    ld[l]._ticksPerUpdate = 2
    ld[l]._temporalHorizon = 2
    ld[l]._alpha = 0.1
    ld[l]._beta = 0.1
    ld[l]._delta = 0.0

resizedWidth = 64
resizedHeight = 48

motorChunkSize = int(5)
hiddenChunkSize = int(6)
SDRSizeDiv = int(1)

hiddenWidth = resizedWidth
hiddenHeight = int(resizedHeight * 2 / 3) - 3

sdrWidth = int(hiddenWidth / SDRSizeDiv)
sdrHeight = int(hiddenHeight / SDRSizeDiv)

numChunksInX = int(sdrWidth / hiddenChunkSize)
numChunksInY = int(sdrHeight / hiddenChunkSize)
numChunks = numChunksInX * numChunksInY
bitsPerChunk = hiddenChunkSize * hiddenChunkSize

print("SDR Width x Height: " + str(sdrWidth) + " " + str(sdrHeight))

h = eogmaneo.Hierarchy()
enc = eogmaneo.ImageEncoder()

# Hierarchy and pre-encoder saved state filenames
saveName = "SDCSaveSobel.eohr"
saveNameEnc = "SDCSaveEncSobel.txt"

if os.path.isfile(saveName) and loadExisting:
    print("Loading existing hierarchy...")

    h.load(saveName)
    enc.load(saveNameEnc)

else:
    print("Creating new hierarchy...")

    h.create([(sdrWidth, sdrHeight), (motorChunkSize, motorChunkSize)], [hiddenChunkSize, motorChunkSize], [False, True], ld, 41)
    enc.create(hiddenWidth, hiddenHeight, sdrWidth, sdrHeight, hiddenChunkSize, 6, 1234)

print("Created pre-encoder and hierarchy.")

trainMode = True
enabled = False

trimming = 0.0
powerScalar = 0.5

targetSteer = 0.0
targetDrive = 0.0
targetMode = False

steer = 0
drive = 0
mode = 0

joymodePrev = False

saveImgPrev = False
saveHPrev = False
loadHPrev = False

imgIndex = 0

endProg = False

print("")
print("Controls:")
print("The `A` button toggles between training and prediction modes.")
print("The `B` button saves the current camera image.")
print("The `X` button saves the current state of the hierarchy.")
print("The `Y` button exits the script.")
print("")
print("The joystick controls left/right steering.")
print("Trigger buttons apply forward/backward drive.")

############################
# Loop until the 'Y' button is pressed

while not endProg:
    try:
        timeStart = pygame.time.get_ticks()

        ############################
        # Check Pygame for exit conditions

        for event in pygame.event.get():
            if event.type == pygame.JOYBUTTONDOWN and joy.get_button(3) == 1:
                endProg = True

            if event.type == pygame.QUIT:
                endProg = True

        keys = pygame.key.get_pressed()

        if keys[pygame.K_ESCAPE]:
            endProg = True

        ############################
        # Receive Steam controller data

        joydrive = (joy.get_axis(5) * 0.5 + 0.5) - (joy.get_axis(2) * 0.5 + 0.5)
        joysteer = joy.get_axis(0)

        joymode = joy.get_button(0)

        steer = joysteer
        drive = joydrive

        if joymode and not joymodePrev:
            mode = not mode

        joymodePrev = joymode

        moving = drive > 0.05

        training = not mode

        ############################
        # Grab an image from the camera

        visData = np.empty((camHeight, camWidth, 3), dtype=np.uint8)

        camera.capture(visData, "rgb", use_video_port=True)

        if resizedWidth != camWidth or resizedHeight != camHeight:
            visData = cv2.resize(visData, (resizedWidth, resizedHeight), interpolation=cv2.INTER_AREA)

        visData = visData[resizedHeight - int(hiddenHeight):, :, :]

        # Convert to grey scale
        visDataGrey = 0.333 * ((visData[:, :, 0].T / 255.0) + (visData[:, :, 1].T / 255.0) + (visData[:, :, 2].T / 255.0))

        # Apply optional Sobel filtering, and ravel to a 1D list
        filtered = visDataGrey.T.ravel().tolist()#eogmaneo.sobel(visDataGrey.T.ravel().tolist(), hiddenWidth, 0.0, esystem, 8)

        # Send the filtered camera image into the ImageEncoder
        useSDR = enc.activate(filtered, esystem)

        enc.learn(0.1, esystem)

        ############################
        # Create a sparse chunked representation from the steering and drive values
        left = min(1.0, max(-1.0, drive * 0.5 + drive * steer * 0.5))
        right = min(1.0, max(-1.0, drive * 0.5 - drive * steer * 0.5))

        motorSDR = [int((steer * 0.5 + 0.5) * (motorChunkSize * motorChunkSize - 1) + 0.5)]

        useMotorSDR = motorSDR

        # In inference mode, use the hierarchy next predicted steering values
        if not training:
            useMotorSDR = h.getPrediction(1)

        if not training or moving:
            h.step([useSDR, useMotorSDR], esystem, training and moving)

        sendLeftMotor = left
        sendRightMotor = right

        # In inference mode, use the hierarchy prediction to drive
        # the motors (instead of the steam controller)
        if not training:
            predMotorIndex = h.getPrediction(1)[0]

            drive = 0.65

            predSteer = predMotorIndex / float(motorChunkSize * motorChunkSize - 1) * 2.0 - 1.0

            sendLeftMotor = min(1.0, max(-1.0, drive * 0.5 + drive * predSteer * 0.5))
            sendRightMotor = min(1.0, max(-1.0, drive * 0.5 - drive * predSteer * 0.5))

        # Apply corrective trimming to the motor drive values
        trimMulLeft = 1.0 - max(0.0, -trimming)
        trimMulRight = 1.0 - max(0.0, trimming)

        # Set the speed of each motor
        explorerhat.motor[0].speed(int(sendLeftMotor * trimMulLeft * powerScalar * 100))
        explorerhat.motor[1].speed(-int(sendRightMotor * trimMulRight * powerScalar * 100))

        ############################

        # Save out the current camera image?
        if joy.get_button(1) and not saveImgPrev:
            cv2.imwrite("img" + str(int(imgIndex)) + ".png", visData[:, :, ::-1])

            print("Saved image.")

            imgIndex += 1

        # Save out the current state of the hierarchy?
        if joy.get_button(2) and not saveHPrev:
            print("Saving hierarchy...")

            h.save(saveName)
            enc.save(saveNameEnc)

            print("Saved hierarchy.")

        saveImgPrev = joy.get_button(1)
        saveHPrev = joy.get_button(2)

        timeEnd = pygame.time.get_ticks()

        deltaTime = timeEnd - timeStart

        pygame.time.delay(max(0, 100 - deltaTime))

    except KeyboardInterrupt:
        endProg = True
        break

pygame.quit()

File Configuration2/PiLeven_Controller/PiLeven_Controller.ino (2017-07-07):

/*
  EOgmaDrive
  Copyright(c) 2017 Ogma Intelligent Systems Corp. All rights reserved.

  This copy of EOgmaDrive is licensed to you under the terms described
  in the EOGMADRIVE_LICENSE.md file included in this distribution.
*/

#include <Wire.h>

typedef enum EState {
  WARM_UP = 0,
  TRAINING_MODE = 1,
  PREDICTION_MODE = 2
};

int state = WARM_UP;
unsigned long startTime = 0;
const long warmUpTime = 1000; //milliseconds

int ledPin = 13;

int i2cAddr = 4;            // Slave addr: 4
unsigned char i2cRxBufferLen;
unsigned char i2cRxBuffer[BUFFER_LENGTH];

int steeringInputPin  = 9;  // From RF unit
int steeringOutputPin = 8;  // To steering servo
int throttleInputPin  = 10; // From RF unit
int throttleOutputPin = 11; // To ESC unit

int currSteeringPinState = 0;
int prevSteeringPinState = 0;
int currThrottlePinState = 0;
int prevThrottlePinState = 0;

int steeringHiCount = 0;
int steeringLoCount = 0;
int totalSteeringCount = 0;

int throttleHiCount = 0;
int throttleLoCount = 0;
int totalThrottleCount = 0;

long actualSteeringValue = 45;
long predictedSteeringValue = 45;
long actualThrottleValue = 45;
long predictedThrottleValue = 45;


void setup() {
  startTime = millis();

  // Setup i2c interface with RPi
  Wire.begin(i2cAddr);
  Wire.onReceive(i2cReceiveEvent);
  Wire.onRequest(i2cTransmitEvent);

  // Setup UART to XBee
  Serial.begin(9600);
  Serial.println("");
  
  // Setup I/O pins
  //pinMode(steeringInputPin, INPUT);
  //pinMode(steeringOutputPin, OUTPUT);
  
  //pinMode(throttleInputPin, INPUT);
  //pinMode(throttleOutputPin, OUTPUT);
  
  // Use LED for debug
  pinMode(ledPin, OUTPUT);
  digitalWrite(ledPin, LOW);
}


void loop() {
  // Grab input states
  prevSteeringPinState = currSteeringPinState;
  currSteeringPinState = digitalRead(steeringInputPin);
  
  // Throttle forwarding
  prevThrottlePinState = currThrottlePinState;
  currThrottlePinState = digitalRead(throttleInputPin);
  
  switch (state) {
    case WARM_UP:
      if ((millis() - startTime) >= warmUpTime) {
        // Tell Pi-Top warm up is over
        Serial.println("Warm-up complete");
        digitalWrite(ledPin, HIGH);

        state = TRAINING_MODE;
        Serial.println("Mode: Training");
      }
      break;
      
    case TRAINING_MODE:
      // Count pin states
      if (currSteeringPinState == 1)
        steeringHiCount++;
      else
        steeringLoCount++;

      if (currThrottlePinState == 1)
        throttleHiCount++;
      else
        throttleLoCount++;

      // Capture low state transitions
      if (currSteeringPinState == 1 && prevSteeringPinState == 0) {
        actualSteeringValue = steeringHiCount;
        totalSteeringCount = steeringHiCount;
        steeringHiCount = 0;
      }

      if (currThrottlePinState == 1 && prevThrottlePinState == 0) {
        actualThrottleValue = throttleHiCount;
        totalThrottleCount = throttleHiCount;
        throttleHiCount = 0;
      }

      // Capture high state transitions
      if (currSteeringPinState == 0 && prevSteeringPinState == 1) {
        totalSteeringCount += steeringLoCount;
        steeringLoCount = 0;
      }

      if (currThrottlePinState == 0 && prevThrottlePinState == 1) {
        totalThrottleCount += throttleLoCount;
        throttleLoCount = 0;
      }

      // Forward to steering servo and ESC
      digitalWrite(steeringOutputPin, currSteeringPinState);
      digitalWrite(throttleOutputPin, currThrottlePinState);
      break;

    case PREDICTION_MODE:
      if (totalSteeringCount <= predictedSteeringValue) {
        steeringHiCount++;
        digitalWrite(steeringOutputPin, HIGH);
      }
      else {
        steeringLoCount++;
        digitalWrite(steeringOutputPin, LOW);
      }
        
      totalSteeringCount++;
      if (totalSteeringCount > 308)
        totalSteeringCount = 0;

      digitalWrite(throttleOutputPin, currThrottlePinState);
      break;
  }
}

void i2cReceiveEvent(int numBytes) {
  i2cRxBufferLen = (numBytes <= BUFFER_LENGTH) ? numBytes : BUFFER_LENGTH;
  
  for (int i = 0; i < i2cRxBufferLen; i++) {
    // get the byte sent from the RPi
    i2cRxBuffer[i] = Wire.read();
  }
 
  if (i2cRxBuffer[0] == 97) { //'a'
  }
  else
  if (i2cRxBuffer[0] == 98) { //'b'
  }
  else
  if (i2cRxBuffer[0] == 99) { //'c'
    predictedSteeringValue = i2cRxBuffer[1] | i2cRxBuffer[2]<<8;
  }
  else
  if (i2cRxBuffer[0] == 100) { //'d'
    predictedThrottleValue = i2cRxBuffer[1] | i2cRxBuffer[2]<<8;
  }
}

void i2cTransmitEvent() {
  if (i2cRxBuffer[0] == 97) { //'a'
    Wire.write(actualSteeringValue);
  }
  else
  if (i2cRxBuffer[0] == 98) { //'b'
    Wire.write(actualThrottleValue);
  }
}

// Check for XBee serial input (from Pi-Top)
void serialEvent() {
  char inChar = 0;

  while (Serial.available()) {
    // get the new byte:
    inChar = (char)Serial.read(); 
  }
  
  if (inChar == 't' || inChar == 'T') {
    state = TRAINING_MODE;
    Serial.println("Mode: Training");
    digitalWrite(ledPin, HIGH);
  }
  if (inChar == 'p' || inChar == 'P') {
    predictedSteeringValue = actualSteeringValue;
    totalSteeringCount = 0;
    state = PREDICTION_MODE;
    Serial.println("Mode: Prediction");
    digitalWrite(ledPin, LOW);
  }
  if (inChar == 's' || inChar == 'S') {
    Serial.print("Steering: A=");
    Serial.print(actualSteeringValue);
    Serial.print(" P=");
    Serial.print(predictedSteeringValue);
    Serial.print(" Throttle: A=");
    Serial.print(actualThrottleValue);
    Serial.print(" P=");
    Serial.println(predictedThrottleValue);
  }
  if (inChar == 'v' || inChar == 'V') {
    Serial.print("Steering: [");
    Serial.print(steeringHiCount);
    Serial.print(", ");
    Serial.print(steeringLoCount);
    Serial.print("], ");
    Serial.print(totalSteeringCount);
    Serial.print(" Throttle: [");
    Serial.print(throttleHiCount);
    Serial.print(", ");
    Serial.print(throttleLoCount);
    Serial.print("], ");
    Serial.println(totalThrottleCount);
  }
}
